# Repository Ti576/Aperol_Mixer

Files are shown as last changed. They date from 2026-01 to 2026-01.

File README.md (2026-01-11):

# Aperol_Mixer
The Instagram Famous Aperol Mixer

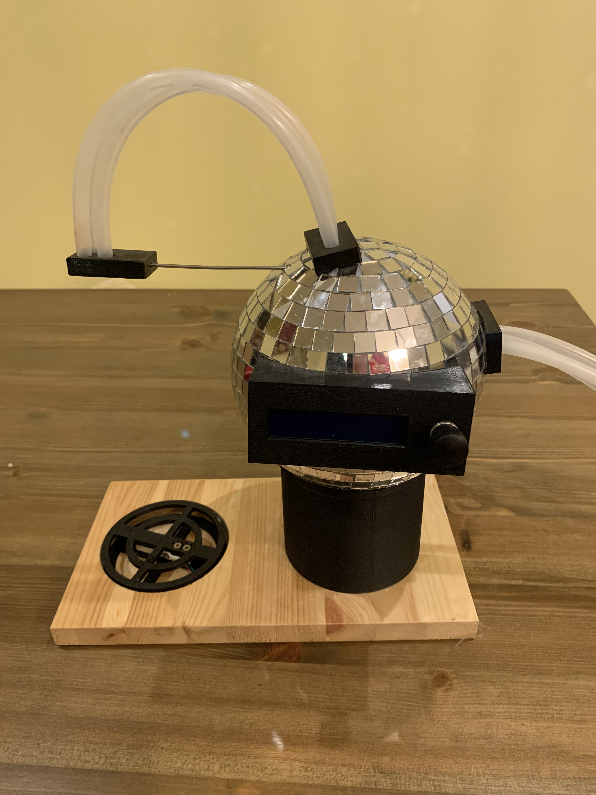
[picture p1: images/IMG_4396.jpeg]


You're probably here from following the link on kate_ivy_peace's instagram showing the Aperol dispenser I made her https://www.instagram.com/kate_ivy_peace/reel/DRjfJR4iDU8/

The following are some fairly rubbish instructions on how to make yourself a version of this wonderful device.

# BoM:

* 3 diaphragm pumps.  This is the basis of the whole thing.  The diameter of the pumps you use will drive the size of everything elseI used these but others are available - https://www.aliexpress.com/item/1005008389360033.html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

* Arduino nano

* Solderless Breadboad small enough to fit in the footprint that you use.  I had to dremel the corners off mine

* 16x2 i2C LCD display

* Rotary encoder.  Mine was out of a BMW M5, funnily enough.

* Load cell to detect if there is a glass in place to catch the aperol.  I used a 750g one, you might need to change this if you are using huge glasses and delivering pints of cocktail.  The code assumes you are using an HX711 based loadcell.

* A reasonable amount of 3d printer filament

* Inserts and screws for the 3d prints

* Random wires, flyback diodes for the motors and resistors

* 3 MOSFETS to drive the motors.  I used IRF3205s

* 12v Power supply and matching plug socket

* A suitable block of wood for the base

* A glitter ball!  Bear in mind that you'll be using it upside down so you don't want a vase or anything with a flat base as it'll look wierd.  I ended up using one intended as a hanging basket.

* A bicycle spoke or similar stiff wire

* Food safe silicone hose, mine was 6mm id but it needs to suit your pumps

# Stream of conciousness 'instructions':

## CAD Files

The CAD files are in the 'OpenSCAD' folder.  You will need to open them in OpenSCAD, make any changes (hopefully the files are reasonably self documenting) then export them as stls at which point you con import them into your favourite slicing program.

The files can be divided into 3 main areas:

1. The glass stand:
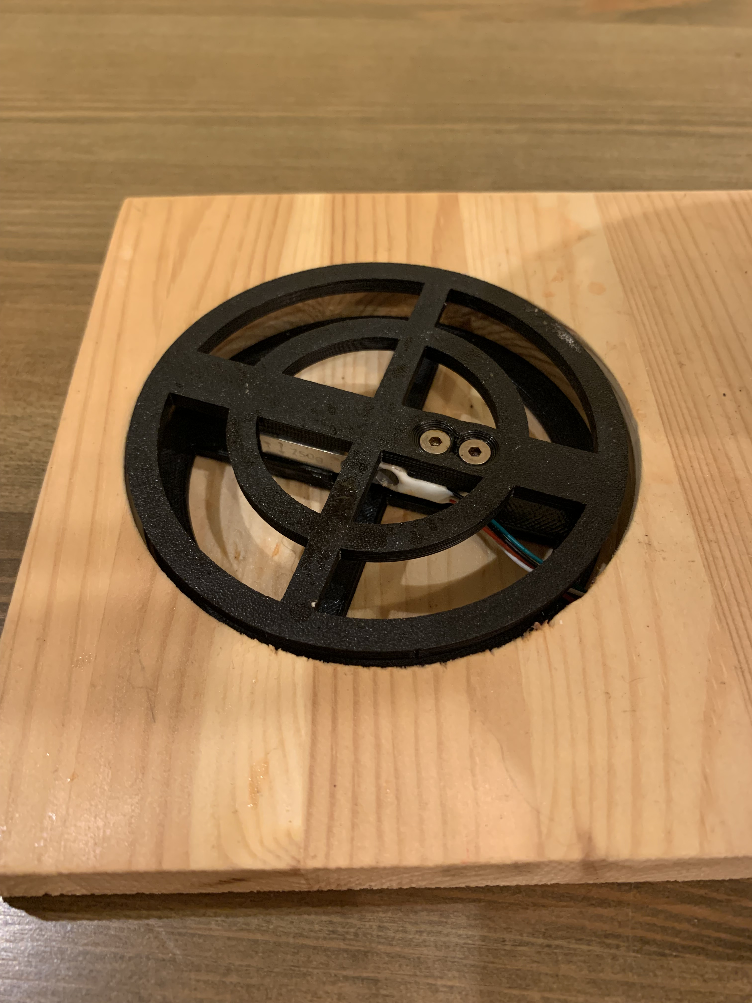
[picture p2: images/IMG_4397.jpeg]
The glass stand


This is made up of one each of DrinkDispenserGlassStand.scad and DrinkDispenserGlassStand2.scad.  The GlassStand2 file has a second circle to stop small glasses toppling over.  The strain gauge can then be attached between the two.

I routed out the circular recess on the base for the glass stand to fit into, the file RouterTemplate.scad allows you to print a template to guide the router, you may need to do some maths to allow for your chosen glass stand diameter, router bush diameter and router cutter diameter.  That is left as an excercise for the reader.  Alternatively I suppose you could use two thicknesses of ply and use a hole saw to cut an appropriate size hole in the top one before glueing them togther.

2. The base and motor holder:

BaseStand.scad - This screws to the base and the cylinderical base fits over it.  If I get round to a version 2, I'd notch it to allow the USB to be plugged to in the arduino more easily.  If you look on the pictures I've done this with a dremel on the orginal.  You might need to play with tolerances to get it to fit tightly but not too tightly inside the base.
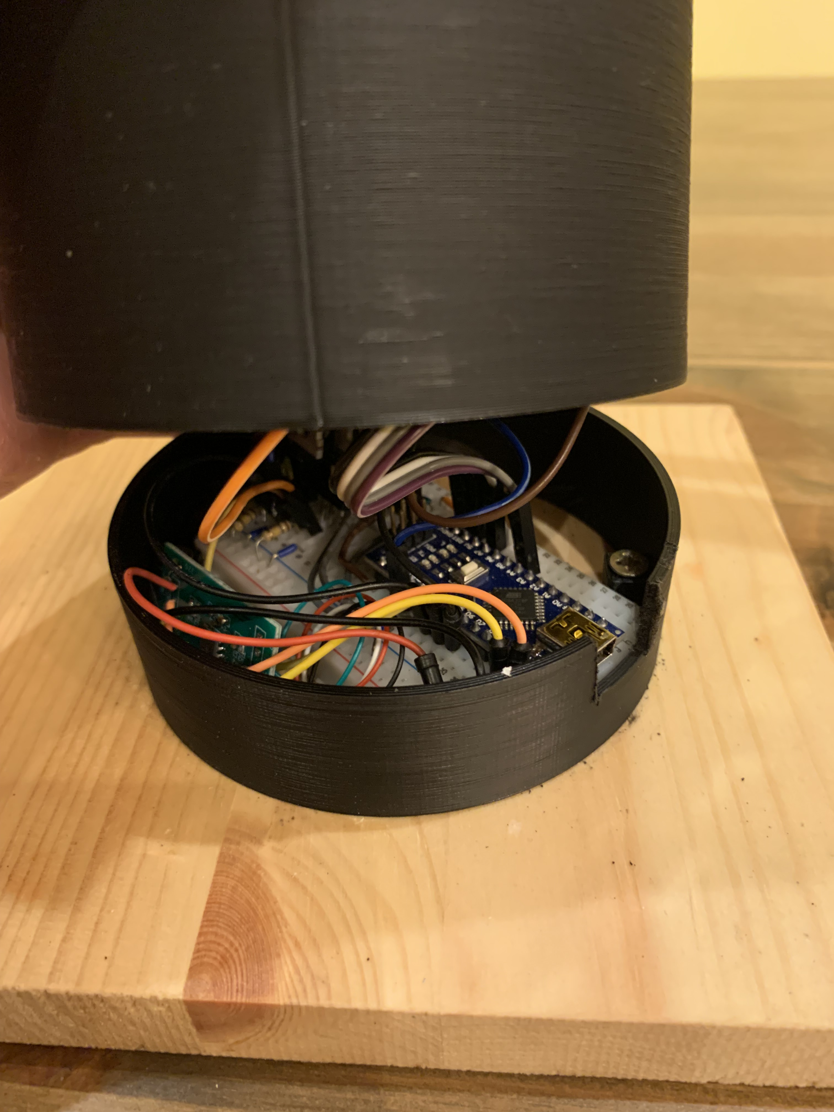
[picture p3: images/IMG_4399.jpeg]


DrinkDispenserBase.scad - This is the main cylinderical base.  The diameter will need to be adjusted to match the glitter ball you're using.  There is a ridge of the outside to support the glitter ball and one on the inside to support the motor mount
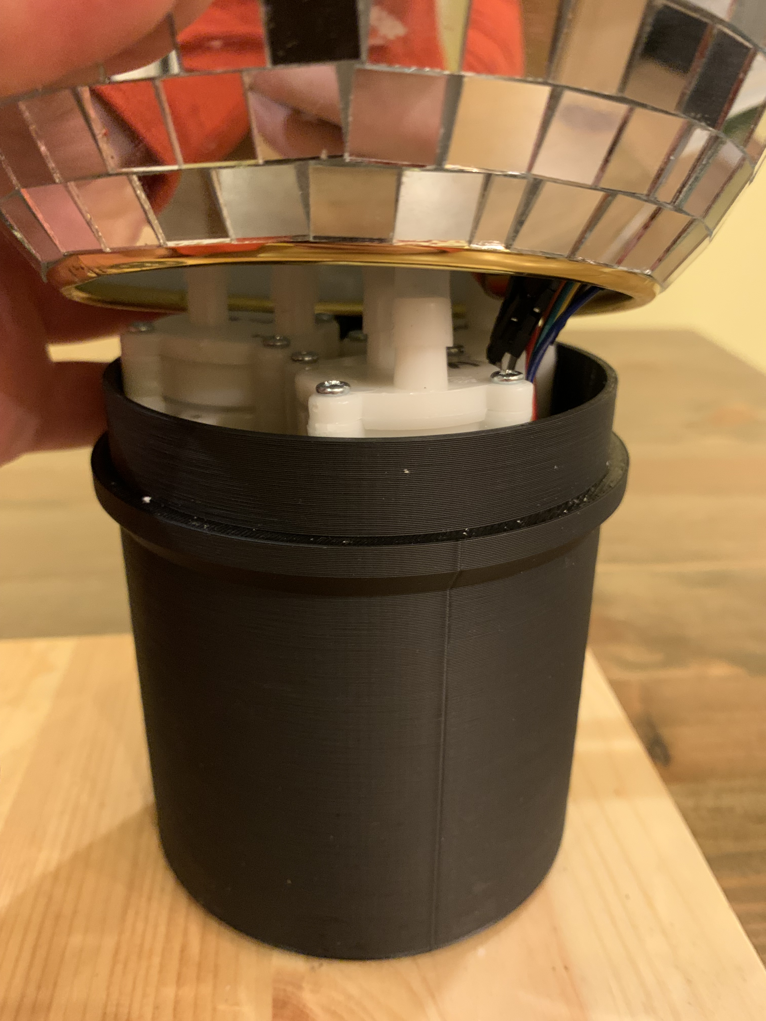
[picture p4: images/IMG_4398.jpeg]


DrinkDispenserMotorMount.scad - The motors sit in this, there are labels to identify each motor.  Again, you'll need to alter the dimensions as appropriate.  I printed this in TPU to get a bit of grip on the motors, not sure if it was needed.

3. The fittings for the glitter ball.  You will need to drill/cut holes in the glitter ball to let pipes and wires in and out:

DisplayHolder V2.scad - The holder for the display and rotary encoder.  Again, you'll need to adjust dimensions and the curvature of the cutout for the glitterball.  There are fittings for threaded inserts to retain the display and to screw the display holder onto the glitterball.  The file 'DisplayHolder Jig.scad' can be used as a jig to dril the mounting holes in the glitterball as you can't drill from the inside of the glitterball (or I couldn't!)
 
PipeInlet.scad and PipeOutlet.scad -  Do what they say on the tin, these can be glued on to the glitter ball after you've cut suitable holes for the pipes.  The Pipeinlet has letters to identify what tube goes into what drink

PipeHolder.scad - This can be supported by a bicycle spoke or other stiff wire to hold the end of the outlet pipes over the glass.

## Wiring

The wiring for the arduino is obviously in the arduino code so this should be altered if you want to change pin assignments.

Arduino Power:  
12v input to VIn  
Ground to Gnd  

LCD Display:  
I2C LCD SDA to A5  
I2C LCD SCL to A4  
I2C LCD Ground to Gnd  
I2C LCD VCC to 5v  

Rotary Encoder:  
Pin 1 (Ground) to Gnd  
Pin 2 (Button 1) to Gnd  
Pin 3 (Button 2) to D1  
Pin 4 (rotary 1) to D2  
Pin 5 (rotary 2) to D3  
Pin 6 (VCC) to 5v  
My rotary encoder needed a number of pull down resistors, look at the data sheet for the one you are using.

Strain Gauge:  
Glass detection strain gauge DT to D12  
Glass detection strain gauge SCK to D13  
VCC to 5v  
Gnd to Gnd  

Motor Control Pins connect to MOSFET gate pins:  
Aperol Pump Control to D4  
Prosecco Pump Control to D5  
Lemonade Pump Control to D6  

The motor +ves should be wired to 12v and the ground via the MOSFET drain pin along the lines of:
MOSFET Wiring

## Arduino Program

The Arduino code is in the 'arduino' folder, if you are a programmer then please let me know if I've made any catatsrophic errors.  

You will need a number of libraries installed for the code to compile:
* HX711 by Bogdan Necula
* LCD I2C by Frank Hafele
* Encoder by Paul Stoffregen
* Wire library that should be built in to the arduino IDE

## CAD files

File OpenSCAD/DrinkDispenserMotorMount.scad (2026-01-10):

//Drink Dispenser Motor Holder//

BaseID=93.5;
HolderThickness=5;
MotorDiameter=27.5;
MotorClearance=5;
MotorMountRadius=(BaseID/2)-MotorClearance-(MotorDiameter/2);
NotchSize=15;

//Create base
difference(){
union() {
    //Basic Holder Circle
        
        cylinder(HolderThickness, r=BaseID/2);
        
}  
//and then put in the motor holes
//No 1
translate([MotorMountRadius*cos(0),MotorMountRadius*sin(0),-0.1])
cylinder(HolderThickness+0.5,r=MotorDiameter/2);

//Add label 
        translate([-15,5,HolderThickness-1])
            linear_extrude(1.5)
            text(str("Aperol"),size=4,halign="center");


//No 2
translate([MotorMountRadius*cos(120),MotorMountRadius*sin(120),-0.1])
cylinder(HolderThickness+0.5,r=MotorDiameter/2);

//Add label 
        translate([30,15,HolderThickness-1])
            linear_extrude(1.5)
            text(str("Lemonade"),size=4,halign="center");

//No 3
translate([MotorMountRadius*cos(240),MotorMountRadius*sin(240),-0.1])
cylinder(HolderThickness+0.5,r=MotorDiameter/2);

//Add label 
        translate([-15,-8,HolderThickness-1])
            linear_extrude(1.5)
            text(str("Prosecco"),size=4,halign="center");

//And a notch for wiring
translate([(-BaseID/2),-NotchSize/2,-0.1])
cube([NotchSize,NotchSize,HolderThickness+0.5]);

    
}


$fa = 1;
$fs = 0.4;

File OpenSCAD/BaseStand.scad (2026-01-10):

//Drink Dispenser Base Stand//

MainDiameter=92;
MainHeight=25;
WallThickness=2;

MountTabWidth=8;
InsertDiameter=5;

module MountTab() {
 translate([-MountTabWidth/2,-MountTabWidth/2,-0])   
difference(){
cube([MountTabWidth,MountTabWidth,10]);
translate([MountTabWidth/2,MountTabWidth/2,-0.1])
cylinder(h=15, r=InsertDiameter/2);    
}  
}

//Create base
union(){
difference(){
    //Main Cylinder
        cylinder(h=MainHeight, r=MainDiameter/2); 
        
        translate([0,0,-0.1])
        cylinder(h=MainHeight+5, r=(MainDiameter/2)-WallThickness);
}
translate([MainDiameter/2-MountTabWidth/2-WallThickness,0,0])
MountTab();

translate([-MainDiameter/2+MountTabWidth/2+WallThickness,0,0])
MountTab();

translate([0,-MainDiameter/2+MountTabWidth/2+WallThickness,0])
MountTab();

translate([0,+MainDiameter/2-MountTabWidth/2-WallThickness,0])
MountTab();

}

$fa = 1;
$fs = 0.4;

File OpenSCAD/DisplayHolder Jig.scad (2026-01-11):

//LCD and rotary encoder holder for drink dispenser
$fa = 1;
$fs = 0.4;

OverallWidth=105;
OverallHeight=43;
OverallDepth=50;
WallThickness=2;

EncoderHoleDiameter=10;
LCDScreenWidth=66;
LCDScreenHeight=16;
LCDWallSpacing=8;

EncoderWallSpacing=10;

SphereDiameter=150;
SphereDistance=90;

LCDStandoff=7; //Remember to take off wall thickness!
LCDStandoffWidth=76;
LCDStandoffHeight=31;

SmallInsertOD=6;
SmallInsertID=3.2;
InsertID=4.5;
InsertOD=7;

module prism(l, w, h) {
    polyhedron(// pt      0        1        2        3        4        5
               points=[[0,0,0], [0,w,h], [l,w,h], [l,0,0], [0,w,0], [l,w,0]],
               // top sloping face (A)
               faces=[[0,1,2,3],
               // vertical rectangular face (B)
               [2,1,4,5],
               // bottom face (C)
               [0,3,5,4],
               // rear triangular face (D)
               [0,4,1],
               // front triangular face (E)
               [3,2,5]]
               );}

module MainBody(){
    union(){
    difference(){
    cube([OverallWidth,OverallDepth,OverallHeight]);
    
     //Hollow out cube to wall thickness
    translate([WallThickness,WallThickness,WallThickness])
    cube([OverallWidth-WallThickness*2,(OverallDepth-WallThickness*2)+5,OverallHeight-WallThickness*2]);
    } 
    
    //Mounts to glitterball, prism on base for printability
    //LCD Side - 1 off central
    difference(){
    union(){
    translate([WallThickness,OverallDepth-25,OverallHeight/2-InsertOD/2])
    cube([InsertOD,20,InsertOD]);
    translate([WallThickness,OverallDepth-25-InsertOD,OverallHeight/2+InsertOD/2])
    rotate([0,90,0])
    prism(InsertOD,InsertOD,InsertOD);
    }
    rotate([-90,0,0])
    translate([WallThickness+InsertOD/2,-OverallHeight/2,WallThickness+0.1])
    cylinder(OverallDepth,r=InsertID/2);
    }

    //Mounts to glitterball, prism on base for printability
    //Encoder Side - one top and one bottom
    difference(){
    union(){
        translate([OverallWidth-WallThickness-InsertOD,OverallDepth-25,WallThickness])
    cube([InsertOD,20,InsertOD]);
    translate([OverallWidth-WallThickness,OverallDepth-25-InsertOD,WallThickness])
    rotate([0,270,0])
    prism(InsertOD,InsertOD,InsertOD);   
    }
    rotate([-90,0,0])
    translate([OverallWidth-WallThickness-InsertOD/2,-WallThickness-InsertOD/2,WallThickness+0.1])
    cylinder(OverallDepth,r=InsertID/2);
    }

    difference(){
    union(){
    translate([OverallWidth-WallThickness-InsertOD,OverallDepth-25,OverallHeight-WallThickness-InsertOD])
    cube([InsertOD,20,InsertOD]);
    translate([OverallWidth-WallThickness,OverallDepth-25-InsertOD,OverallHeight-WallThickness-InsertOD])
    rotate([0,270,0])
    prism(InsertOD,InsertOD,InsertOD);  
    }
    rotate([-90,0,0])
    translate([OverallWidth-WallThickness-InsertOD/2,WallThickness+InsertOD/2-OverallHeight,WallThickness+0.1])
    cylinder(OverallDepth,r=InsertID/2);    
    }
}
 }       
    
union(){
difference(){

   MainBody();

    //To Make a jig
    translate([-100,-20,-10])
    cube([500,30,100]);

    //Glitter ball cutout
    translate([OverallWidth/2,SphereDistance,OverallHeight/2])
    sphere(SphereDiameter/2);
    
    
    //LCD Screen Cutout
    //x position 8mm from edge to wall
    translate([LCDWallSpacing+WallThickness,-0.1,OverallHeight/2-LCDScreenHeight/2])
    cube([LCDScreenWidth,WallThickness+0.5,LCDScreenHeight]);
  
    //Rotary Encoder Hole.  X position calcs needed paper working out!
    translate([OverallWidth-WallThickness-EncoderWallSpacing,-0.1,OverallHeight/2])
    rotate([-90,0,0])
    cylinder(WallThickness+1,r=EncoderHoleDiameter/2);
    
    

}
    
    //Antirotation tab for encoder?
    //Encoder Standoff
    
    
    
}

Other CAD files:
OpenSCAD/DisplayHolder V2.scad
OpenSCAD/DrinkDispenserBase.scad
OpenSCAD/DrinkDispsenserGlassStand.scad
OpenSCAD/DrinkDispsenserGlassStand2.scad
OpenSCAD/PipeHolder.scad
OpenSCAD/PipeInlet.scad
OpenSCAD/PipeOutlet.scad
OpenSCAD/RouterTemplate.scad

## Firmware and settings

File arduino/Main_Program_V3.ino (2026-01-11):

//Aperol Spritz Mixer With LCD screen controlled by rotary encoder, strain gauge for glass sensing and 3 diaphragm pumps for dispensing

//Arduino Uno Pin assignments
//A5 = I2C LCD SDA(grey)
//A4 = I2C LCD SCL (purple)
//I2C LCD Ground (black)
//I2C LCD VCC (White)


//Rotary Encoder pin 1 ground (Brown)
//pin 2 to ground (switch feed)
//1 = Rotary Encoder 3 (Button)
//2 = Rotary Encoder 4 (rotary 2)
//3 = Rotary Encoder 5 (rotary 2)
// Rotary encoder 6 +5v

//4 = Aperol Pump Control
//5 = Prosecco Pump Control
//6 = Lemonade Pump Control

//12 = Glass detection strain gauge DT
//13 = Glass detection strain gauge SCK

//General Setup Options

//Drink Proportions, set timings based on glass size
const int Aperol = 2;
const int Prosecco = 6;
const int Lemonade = 2;

//Calibration for pump performance.  1 pump pumps 570ml in 15 seconds -> 38ml/s ish
unsigned int PumpRate = 38; //ml/s
unsigned long Time_Factor = 1000/((Aperol + Lemonade + Prosecco) * PumpRate);

//Glass size in ml
int Glass_Size = 150;  //default glass size
int Min_Glass_Size = 50;
int Max_Glass_Size = 550;
int Size_Increment = 25;
char Glass_Output[16]  = "";

//Declarations for LCD Screen, encoder and strain gauge
// include the library code:

#include <LCD-I2C.h>
#include <Wire.h>
#include <Encoder.h>
#include "HX711.h"

// HX711 circuit setup
const int LOADCELL_DOUT_PIN = 11;
const int LOADCELL_SCK_PIN = 12;
HX711 scale;

// initialize the LCD Screen
LCD_I2C lcd(0x27, 16, 2); // Default address of most PCF8574 modules, change according

//Declarations for rotary encoder
// Change these two numbers to the pins connected to your encoder.
//   Best Performance: both pins have interrupt capability
//   Good Performance: only the first pin has interrupt capability
//   Low Performance:  neither pin has interrupt capability
Encoder myEnc(2, 3);
//   avoid using pins with LEDs attached

//Timers
unsigned long Pump_Timer = 0;


const int ButtonPin = 1;
long oldPosition = 0;
bool ButtonPosition = 1;
bool OldButtonPosition = 1;

//Declarations for motor output
const int Aperol_Pump = 4;
const int Prosecco_Pump = 5;
const int Lemonade_Pump = 6;

//Glass Sensor Inputs
const int Glass_Sensor = 7;
long Strain_Gauge_Reading;
bool Glass_Present = false;


void setup() {

  Serial.begin(57600);

  //Pin for rotary encoder switch
  pinMode(ButtonPin, INPUT_PULLUP);
  myEnc.write(0);

  //Setup LCD
  Wire.begin();
  lcd.begin(&Wire);
  lcd.display();
  lcd.backlight();

  //Set up motor pins
  pinMode(Aperol_Pump, OUTPUT);
  pinMode(Prosecco_Pump, OUTPUT);
  pinMode(Lemonade_Pump, OUTPUT);
 
  //Glass sensor pin
  pinMode(Glass_Sensor, INPUT);

  //loadcell for glass detection
  scale.begin(LOADCELL_DOUT_PIN, LOADCELL_SCK_PIN);
}

void Check_Pump_Time(int Pin_Number, unsigned long Run_Time){
//if pump has been running for run_time then turn it off
  if (millis() - Pump_Timer >= Run_Time) {

    digitalWrite(Pin_Number, LOW);
  }

}

bool Check_Glass_Present(){
  Strain_Gauge_Reading = scale.read();
  //Serial.println(Strain_Gauge_Reading);
  if (Strain_Gauge_Reading < -100000) {
    return true;
  }
  else{
    return false;
  }
}

void loop() {

  //Serial.print("Loop");

  Glass_Present = Check_Glass_Present();  
  if (Glass_Present == false) {
    //Set display and stop pumps if they're running

    lcd.setCursor(0, 0);
    lcd.print("No Glass Present");
    lcd.setCursor(0,1);
    lcd.print("                ");
    digitalWrite(Prosecco_Pump, LOW);
    digitalWrite(Lemonade_Pump, LOW);
    digitalWrite(Aperol_Pump, LOW);

  }
  else{
 
    lcd.setCursor(0, 0);
    lcd.print("Set Glass Size  ");    
    lcd.setCursor(0,1);
    snprintf(Glass_Output, sizeof(Glass_Output),"%d ml %-16s", Glass_Size,"");
    lcd.print(Glass_Output);

    //Has button been pressed (actually fires on release)
    // ***********   needs some debounce! ***************
    ButtonPosition = (digitalRead(ButtonPin));
    if ((ButtonPosition == 1 && OldButtonPosition == 0) && !(digitalRead(Prosecco_Pump) || digitalRead(Lemonade_Pump) || digitalRead(Aperol_Pump))) {
      //Button Pressed and no pumps already running
      //Start the pumps and the pumnp timer
      digitalWrite(Aperol_Pump, HIGH);
      digitalWrite(Lemonade_Pump, HIGH); 
      digitalWrite(Prosecco_Pump, HIGH);  
      Pump_Timer = millis();
    }
    OldButtonPosition = ButtonPosition;

  //See if we need to stop any pumps
    Check_Pump_Time(Aperol_Pump, Aperol * Time_Factor * Glass_Size); 
    Check_Pump_Time(Lemonade_Pump, Lemonade * Time_Factor * Glass_Size);
    Check_Pump_Time(Prosecco_Pump, Prosecco * Time_Factor * Glass_Size);


  //Set drink sixe if encoder is changed
    long newPosition = myEnc.read();
    if (newPosition > oldPosition && Glass_Size < Max_Glass_Size) {
        Glass_Size = Glass_Size + Size_Increment;
    }
    if (newPosition < oldPosition  && Glass_Size > Min_Glass_Size) {
        Glass_Size = Glass_Size - Size_Increment;
    }
    oldPosition = newPosition;
  }


}

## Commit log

2026-01-10 OpenSCAD files for 3d printed components
    [BaseStand.scad, DisplayHolder V2.scad, DrinkDispenserBase.scad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]
2026-01-10 Upload arduino source code
2026-01-10 Update README.md
    Trying to get the BoM list working
